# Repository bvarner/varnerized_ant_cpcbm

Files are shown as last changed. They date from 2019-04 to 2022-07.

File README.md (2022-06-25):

# Varnerized ANT Compact PCB Maker

Since first coming across the [ANT](https://www.youtube.com/channel/UCX44z-SSL7LzcB4xxgUdHHA) project, I've wanted to make one. However there are some esoteric hardware choices in the base project that seem to prioritize form over function and cost.
As a hobbiest, my primary concerns are not asthetics as much as cost and component availability.

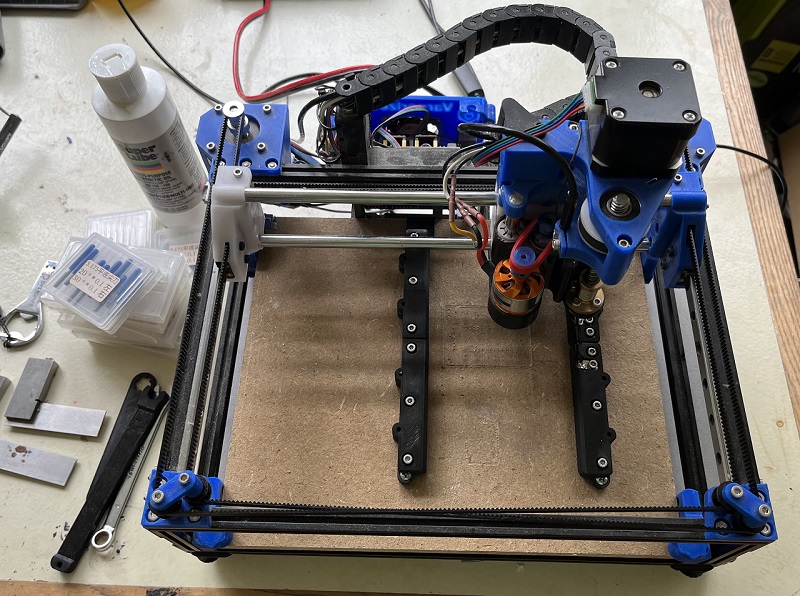
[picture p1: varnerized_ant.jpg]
Varnerized Ant


## Varnerizations
1. Created a parametric (parameterized) reimplemenation of the [bridge & head in Fusion 360](https://a360.co/3jG9QqE). Fusion Archive and STEP export included.
2. 8MM Linear Rods & LM8UU linear bearings. 
    * Sacrificed 4mm of Y axis travel to allow for wall thicknesses to be reasonable with 15mm bores.
    * Added 1mm to the height to the left-right bridge and center bridge, added 1mm separation betweeen centers of the x-axis rails.
3. Bridge Core is now One Piece.
    * Captive M3 Hex Nuts allow the use of (3) M3x30 and (3) M3x40 screws instead of the original BOM spec for (3) M3 threaded rods cut to length.
    * Linear bearing holes are _barely_ oversized, allowing for the M3x30 screws to act as compression mechanisms to hold the bearings.
    * Expansion / Compression cut for linear bearings. M3 screws holding together the bridge act as compression points to hold the bearings snug.
4. Use of sub-mini microswitches for limit-switches. No need to purchase specific orientation limit switch modules, especially when the connections to the grbl board aren't making use of pull resistors.
5. NEMA17 Stepper Motors
    * Reinforced COREXY Mounts based upon [this design on Thingiverse](https://www.thingiverse.com/thing:3590519) eliminate the need for extra retainers from the thingiverse part.
    * GT2 belt-driven Z-Axis. [140 Tooth 2GT-6](https://www.amazon.com/140-2GT-6-Timing-Belt-Closed-Loop/dp/B014QJBVOY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) allows for swapping out gear ratios to adjust for different leadscrew pitches.
6. TR8 Leadscrew (with 8mm pitch) for Z-Axis
7. Remodeled and removed unnecessary holes from the bridge left and right.
8. Belt holder holds a captive nut to secure it to the bridge.
9. Easily Obtainable [D2826 1000kv](https://www.amazon.com/dp/B089YPSYD6?psc=1&ref=ppx_yo2_dt_b_product_details) BLDC motor.
    * 3d-printed TPU (shore 95A) drive belt.
    * 3d-printed PolyCarbonate drive pulleys. (Eliminated the stop-collar on the spindle)
10. Use of an open cable chain, and necessary mounts to the bridge & electronics case.
    * Use of 40mm screws on the electronics case, further customizations to make it easier to fit panel-mount through-hole jacks.
    * modified the electronics panel to use a rectangular switch and a XT-60H connector for power.
11. 3d printed GT2 pulleys.
    * I have since switched to machine pulleys, as I was diagnosing some movement precision issues. Changing to machined pulleys had no noticeable effect. My issues were elsewhere.
12. PCBLock <-> Frame connection.
    * Changed orientation of the contact strips to vertical -- allowing for more 'slop' between alignment in both the x, and z axis.
    * Contact is no longer dependent upon the thickness of the spoil-board, so thinner / thicker board will still contact well.
    * I used 4mm strips of 0.15mm thick nickel strip. (cut from an 8mm wide strip commonly used in 18650 battery packs)

### Analysis and Evaulation Guidelines

In making my decisions about what to 'Varnerize' vs. purchase and stick to the plans I weighed things based upon:

* What's already in my component drawers or easily obtainable given current supply chain and production limitations. Prioritized functional available parts over form.
* What I can reasonably 3d-print and combine with something else already in my component drawers. Prioritized self fabrication over purchasing produced parts.
* Functional Accuracy. Modifications will prioritize accuracy over workable size. I was willing to reduce the work area. I didn't have to.
* Build cost.

### Specific investigations undertaken

* NEMA17 steppers in place of the NEMA11s, and in the case of the head, in place of the NEMA 8. I've seen [this top-mounted NEMA 11 modification](https://jplattel.nl/post/2021-03-07-improving-the-ant-head/) which has supplied a surprising amount of 'idea fuel'.
* Bridge segmenting and joinery.
* Use of an Arduino Uno R3 + GRBL board instead of the STM32 based Arm board + GRBL board.
* 8mm Rods and LM8UU bearings instead of the 6mm rods and LM6UU bearings.
* 3d printable pulleys based around 683ZZ bearings. As of 10/2021 I was able to obtain a 20 pack of these bearings for $10. Sourcing the appropirate number of 16-tooth pulleys would have cost more than the 20 pack of bearings.
* Overhangs in some parts (which seem to be dimensionally important) should have 'snap-off' supports.
* Use of a TR8x8 leadscrew, along with a GT2 closed loop belt and pulley system for Z-Axis motion. I have a few of these belts laying around from converting my prusa-style printer to a [Skelestruder](https://jltxplore.dozuki.com/c/Skelestruder_for_Prusa_MK3) extruder.

### Purchased items I did not 'skimp' on:
* MakerBeam! I bought the starter kit, and the tee nuts. I _did_ investigate printing the tee nuts and had workable facimilies printed with a 0.4mm nozzle but was not confident about the long-term use of the plastic tee-nuts.
* Linear rails. Experience from building 3d printers told me this was worth it.
* LM8UU Drylin Bushings. Because LM8UU ball bearings that are affordable are rubbish. I've been using drylin on my 3d printer for a year or so now, and it's so much quieter, and has so much less lash that it's just worth it.
* Mochu angular contact bearings & CL6-ER8M spindle.

#### Z-Axis Comparative Analysis
##### NEMA 8 ANT Head
The "Beta" NEMA 8 stepper head design uses a 1.8-degree, 18mN/m (0.018N/cm) holding torque stepper paired with a 4mm leadscrew with a 0.635mm pitch, equating to a 0.003175mm linear resolution per step.
(0.635mm / 200 steps = 0.003175mm). 

The default configuration is to set this to half-stepping, doubling the default ANT resolution to:
(0.635 / 400) = 0.0015875mm

##### NEMA 17 Varnerized Head
I have on hand several 17HS4401 steppers, which are 1.8-degree, 42N/cm holding torque, and TR8x8 leadscrews with 8mm pitch and anti-backlash nuts.
Un-reduced, this equates to a linear resolution of 0.04mm.
(8 / 200 = 0.04mm) 

In order to increase the resolution, I've selected a 16:52 gear ratio and 140 tooth GT2 timing belt (which I had on hand from building a Skelestruder extruder for my printer).
This brings the effective resolution to:
(8 / (200 * 3.25)) = 0.012307692mm

Enabling 1/4 stepping on the Z-axis motor brings this to:
(8 / (200 * 3.25 * 4)) = 0.003076923mm -- slighty better than the half-stepped NEMA 8.

Enabling 1/8 stepping on the Z-axis will yield:
(8 / (200 * 3.25 * 8)) = 0.001538462mm resolution -- on par with the half-stepped NEMA 8 head.

This equates to a theoretical steps/mm setting of: ~650 steps/mm

Assuming a loss of torque of 29% at the motor shaft (due to microstepping):
At the mottor shaft, the motor provides 29.82N/cm of holding torque.
(42 - (42 * 0.29))
At the lead-screw, this would be 3.25 times higher.
(29.82 * 3.25) = 89.46N/cm

**Conclusion**:

__With 1/8th microstepping, a 1:3.25 gear ratio, and an 8mm pitch leadscrew powered by a 17HS4401 NEMA17, we will exceed the repeatable resolution and torque of the ANT's NEMA8 head design.
Furthermore this part selection will enable using parts I have on hand, cutting the cost to build the head unit considerably.__

## Original ANT Project resources

(https://www.youtube.com/channel/UCX44z-SSL7LzcB4xxgUdHHA)  

The Ant is a project to develop a CNC machine able to realize single and double-layered printed circuit boards.

[Here is a video presentation](https://youtu.be/nVkbG-CYaAA)

The CNC machine is designed to achieve well-determined characteristics:

- Compact
- Low-cost
- Robust
- Scalable
- Easy to build
- Open License

To achieve these properties the following design principle have been adopted:

- Electrical, mechanical and electronics parts have been chosen to be small, low-cost and easily available on the open market or 3D printable
- Mechanical design has been oriented to minimize the space occupied by the components
- Mechanics has been designed to be robust and stress resistant
- Mechanics has been designed so that the external dimensions of the machine may be changed with a minimal change of pieces and no re-design needed.
- Mechanical and electrical designs have taken in account the assembling and disassembling operations, allowing to use easily available tools as screwdrivers, Allen wrenches and a solder for electrical contacts.
- The microcontroller board used to control the CNC machine is inexpensive (~15 $) but is equipped with a powerful STM32 processor and many peripherals.
- The machine control firmware can be loaded with almost no effort, since the microcontroller board has been chosen to have an on-board programmer.
- The control firmware is derived from GRBL v.0.9j, but it is also customized to achieve better performance, taking advantage of the powerful processor, and to be more flexible, since more configuration parameters and features have been added respect to the original firmware

The Ant is an open project, but if you feel like donating a small sum, you are very welcome. Just use the paypal button below.

paypal (https://www.paypal.com/cgi-bin/webscr?cmd=_s-xclick&hosted_button_id=BTRCVPZUZYW2E)

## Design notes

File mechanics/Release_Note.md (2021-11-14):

# 06-11-2021
New release The_Ant_version_1_1_0 with the new NEMA-8 motor as Z-axis. From now on, this head will be considered the stable version. List of updates:  

	* Total_BOM_Ver_1_1_0.xlsx:  
	    - Revisited version of the BOM that integrates the previous BOM with the new parts.

	* head_4p3 replaces head_4p2(copied in release folder from beta one):  
		- new head_4p3 that uses new Z-axis motor. See the BOM for the model of motor.  
	  
	* bridge_2p4_b replaces bridge_2p3_b(copied in release folder from beta one):  
	    - new bridge needed to accomodate the anti-backlash nut of the new Z-axis motor.
		
	* pcb_lock_2p3 replaces pcb_lock_1p0(copied in release folder from beta one):  
	    - the new pcb lock is more robust and adjustable.  
		- integrates part of probe circuit.  
		
	* pcb_lock_frame_to_bed_connection_1p0 added(copied in release folder from beta one):  
	    - new parts of the bed holder needed to integrate the new parts of probe circuit.  
		
	* cable_chain_1p0(copied in release folder from beta one):  
	    - new parts to use drag chain for the cable, substituting the spiral coil used previously.  

# 21-07-2019
New parts released, list of updates:

	* head_4p2 copied in release folder from beta one:
		- previous head_4p2 splitted in head_4p2 and pulley_4p2
		- pulley_4p2. It uses new collar for chuck pulley, if hexagon socket screw doesn't protude from the collar, replace it with a longer one. The file collects chuck pulley, turnigy pulley (3mm shaft) and mystery pulley (2.2mm shaft)
		- spindle motor with outer diameter up to 28mm can now be mounted.
	
	* bridge_2p3_a and bridge_2p3_b:
		- New version of the bridge, more rigid and stable.
		- The *_a it is file related at the unchanged parts from previous version. *_b file it's related to the new parts. They are fully compatible with the older version. If you have printed previous version, print only the *_b parts to update.
		- The bridge is compatible both with 4p1 and 4p2 head versions.
		- Added protection cap.
		- Modified camera holder, now more strong with new lock mechanism. 
		- Added lock holes at the bottom for future features.
		- Reinforced and updated z-motor connection.
	
	* z_motor_tool, useful tool to lock the z-motor shaft to the bridge.

Removed parts:

	* head_4p1
	
	* bridge_2p2

All previous parts are available in The_Ant_version_1_0_0 file.
You can find it in the download section under the "tags" tab.
A new version of BOM is added to keep trak of all changes.
The new pieces require a set of new parts:
	
	* 2 M3x10mm DIN 912 bolt
	* 1 M3x12mm DIN 912 bolt
	* 1 Lock collar(ring) internal diameter 6 mm, external diameter 12mm
	* 2 O-ring inner diameter > 17mm, 1.78mm thick. Innerd diameter to be defined.

# 23-04-2019
Added beta_developments directory, where we share parts not yet released and under test.

# 14-04-2019
Released all step files. 
Added tool for tool bit change (both stl and step).

Bug fixes:
bridge_2p2
	* minor bug fix, camera holder screw holes now deeper
	  to improve the clamping force
	  
head_4p1
	* minor bug fix, chuck pulley base now smaller to prevent
	  friction with bearing

# 31-12-2018

## Scope

Release of mechanical drawings of the Compact PCB Maker. 
This release completes the previous one and comprises the mechanical drawings of the bridge, of the head and of the microcontroller cover. 
The suggestions of the previous release apply also to this one.

# 09-12-2018

## Scope

First release of mechanical drawings of the Compact PCB Maker. 
This is a partial release that comprises all the frame related mechanical drawings. Other parts and corrections will follow in other releases.

## Suggestions

We suggest you to print the parts as they are, because the printing position is designed to enhance the mechanical behavior.

We also suggest you to print with a 0.2 mm layer thickness, 25% of infill, 1.5 mm of wall thickness and extrusion width (also called line width) of 0.5 mm. 

We usually print with PLA but it's not a MUST, you may choose different materials taking in account the properties of the material you want to use. The overall rigidity is needed.

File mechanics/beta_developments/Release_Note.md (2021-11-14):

# 06-11-2021
Removed all the beta parts that are now released in the new stable version The_Ant_version_1_1_0, and the old beta developments that were already obsolete.  

# 06-02-2021
Added <b>head_4p3</b>, an alternative head that uses the NEMA8.  
This head is meant to be used with the released <b>bridge_2p4_b</b> in which there is the anti backlash nut coupled with the motor.  
Added <b>pcb_lock_2p3</b>, an improved version of the previous 2p2.  
Added <b>cable_chain_1p0</b> to better organize the cables that connect the main electronics to the head electronics.  

# 23-04-2019
This is the Beta Developments folder where we share parts not yet released and under test.

Added <b>head_4p2</b>, an head modified to work with the Mistery D2632 blue and red version and brushless with up to 28 mm diameter.

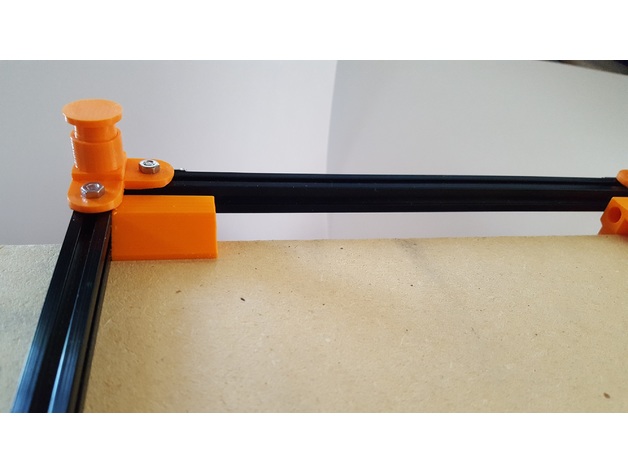
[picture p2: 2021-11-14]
mechanics/frame/Feet/images/b8899656f86f0776ce9d8ce595bd6f32_preview_featured.jpg

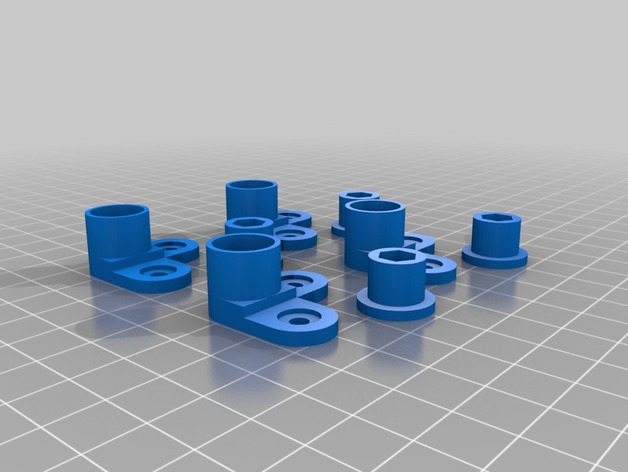
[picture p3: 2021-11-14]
mechanics/frame/Feet/images/fda94fc00cff2d6c941c1d48f293a349_preview_featured.jpg

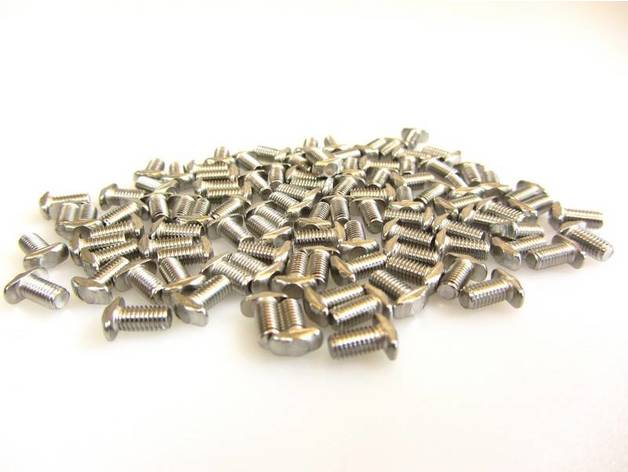
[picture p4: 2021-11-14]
mechanics/frame/Feet/images/6d514020f6163c7c261596526521b55e_preview_featured.jpg

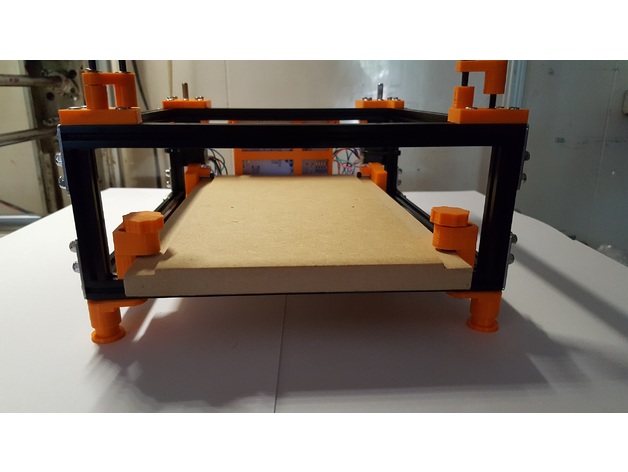
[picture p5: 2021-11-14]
mechanics/frame/Feet/images/d886d0a407164cc080b8dbe587c8e89c_preview_featured.jpg

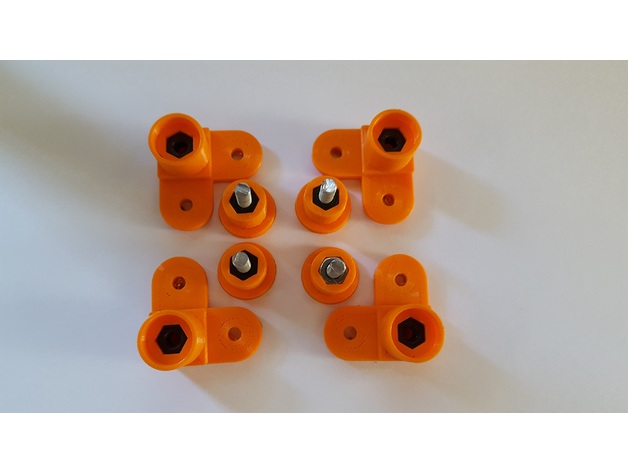
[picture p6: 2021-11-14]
mechanics/frame/Feet/images/ced9a25d92f1a28261a7ffedb2b2fa02_preview_featured.jpg

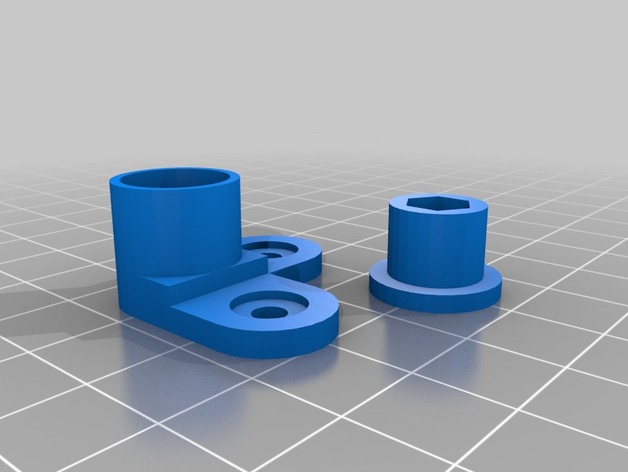
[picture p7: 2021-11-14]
mechanics/frame/Feet/images/ae2aa1dde648d54a71faf4bf8224e998_preview_featured.jpg

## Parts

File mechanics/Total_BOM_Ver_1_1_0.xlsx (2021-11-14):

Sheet: Important NOTE
This is the BOM of The Ant with the new parts released the 6th November 2021, that has the tag "The_Ant_version_1_1_0". If you want to download this frozen version, you may find the relative tag in the tags section of our repository: If you want to know which are the changes in the releases, please read the Release Note in the mechanics folder. | https://bitbucket.org/compactpcbmaker/cpcbm/downloads/?tab=tags

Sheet: Totals Frame BOM
Item | Video 1 | Video 2 | Video 3 | Video 4 | Video 5 | Video 6 | Ver. 1.0.1 | Ver. 1.1.0 | Qty | Info | removed parts
Makerbeam - 10x10mm aluminum profile 200mm (black) | 8 |  |  |  |  |  |  |  | 8 | Makerbeam
Makerbeam - 10x10mm aluminum profile 60mm (black) | 4 |  |  |  |  |  |  |  | 4 | Makerbeam
Makerbeam - 10x10mm aluminum Right Angle bracket | 8 |  |  |  |  |  |  |  | 8 | Makerbeam
M3x6mm square headed bolt | 47 |  |  |  |  |  |  | 9 | 56 | Makerbeam
ISO 7380 M3X4 A2 | 8 |  |  |  | 4 |  | 1 |  | 13 | Makerbeam
Makerbeam T-slot nut | 24 |  |  |  |  |  |  |  | 24 | Makerbeam
M3 self-locking nut | 46 | 9 |  | 2 |  |  |  |  | 57
M3 nut | 4 |  |  |  |  | 8 | 1 | 7 | 20
M5 nut |  |  |  | 1 |  | 2 |  | -1 | 2
M2x8mm DIN 7985 bolt |  |  |  |  | 2 |  |  |  | 2 | used to fix the z-limit switch (maybe you can use M2x10 DIN 7985 instead)
M2x10mm DIN 7985 bolt |  |  |  |  |  |  |  | 4 | 4
M2.5x8mm DIN 912 bolt |  |  |  | 8 |  |  |  |  | 8
M3x6mm DIN 912 bolt | 12 | 9 |  | 2 | 3 |  |  | 13 | 39
M3x8mm DIN 912 bolt |  |  |  |  | 4 |  |  | -2 | 2 | 2 bolts used to lock the nucleo in the case, maybe this can be replaced with 2 bolts M3x10 using double plastic washers (see video 5)
M3x10mm DIN 912 bolt |  | 4 |  |  |  | 8 | 2 | -6 | 8
M3x12mm DIN 912 bolt |  |  |  |  |  |  | 1 | 12 | 13
M3x16mm DIN 912 Bolt | 2 |  |  |  | 4 |  |  |  | 6
M3x20mm DIN 912 Bolt | 8 |  |  | 1 |  |  |  | 1 | 10
M3x25mm DIN 912 bolt |  |  |  | 2 |  |  |  |  | 2
M3x30mm DIN 912 Bolt | 4 |  |  |  |  |  |  |  | 4
M3x50mm DIN 912 bolt |  | 2 |  |  | 4 |  |  |  | 6
M5x16mm hexagon head bolt |  |  |  |  |  | 2 |  |  | 2
Wood screws 3x16mm |  |  |  |  |  | 6 |  | 1 | 7
M3 locking Washer (internal diameter 3mm, external 5.5mm) | 8 | 14 |  |  |  |  |  |  | 22
M3 Washer (internal diameter 3mm, external 7.5mm) | 16 | 10 |  |  |  |  |  |  | 26
GT2 pulley 16T Bore 3mm with bearings | 4 | 2 |  |  |  |  |  |  | 6 | Aliexpress
GT2 pulley No Teeth Bore 3mm with bearings |  | 2 |  |  |  |  |  |  | 2 | Aliexpress
GT2 pulley 16T Bore 5mm height 10mm |  |  |  | 2 |  |  |  |  | 2 | Aliexpress
GT2 6mm Timing belt piece 100 cm |  |  |  | 2 |  |  |  |  | 2 | Aliexpress
Timing Belt Tensioner Spring | 2 |  |  |  |  |  |  |  | 2 | SKU135539-3 FFIO PCK
MGN9H Linear Rail 200 mm | 2 |  |  |  |  |  |  |  | 2 | Aliexpress or Banggood
Bearings lm6uu |  | 8 |  |  |  |  |  |  | 8 | Amazon
Bearing mochu 706C |  | 2 |  |  |  |  |  |  | 2 | Aliexpress
Chrome Plated Rods 6x180mm |  | 2 |  |  |  |  |  |  | 2 | Aliexpress (can be 6x200mm)
Chrome Plated Rods 6x100mm |  | 2 |  |  |  |  |  |  | 2
Threaded Rods M3x100mm |  | 3 |  |  |  |  |  |  | 3
Mechanical Limit Switch Module Vertical |  | 2 |  |  |  |  |  |  | 2 | Aliexpress
Mechanical endstop micro switch with dupont terminal |  |  | 1 |  |  |  |  |  | 1 | Aliexpress
ER8M-C6-60L chuck with 1/8" spring collet |  |  |  | 1 |  |  |  |  | 1 | Aliexpress
~~Lock collar(ring) internal diameter 6 mm, external diameter 12mm~~ |  |  |  | ~~1~~ |  |  |  |  | ~~1~~ | ~~Amazon or Aliexpress. The measured external diameter is 13mm~~
Lock collar(ring) internal diameter 6 mm, external diameter 12mm |  |  |  |  |  |  | 1 |  | 1 | Amazon or Aliexpress. The measured external diameter is 12mm
~~O-ring inner diameter 17mm, 1.78mm thick~~ |  |  |  |  |  | ~~2~~ |  |  | ~~2~~
O-ring inner diameter > 17mm, 1.78mm thick |  |  |  |  |  |  | 2 |  | 2 | Inner diameter to be comfirmed
NEMA-11 JK28HS51-674 |  |  | 2 |  |  |  |  |  | 2 | Aliexpress or Banggood
NEMA 8 with 70mm lead screw 8HY001-70N476 |  |  |  |  |  |  |  | 1 | 1 | Available on Robotdigg site. IMPORTANT NOTE: This line refers only to the stepper motor, not to the anti-backlash nut that must be purchased separately (see the relative line in this file). To buy this motor on the Robodigg page, select the 8HY001-70N476 and put it in the cart. https://www.robotdigg.com/product/644/NEMA8-Linear-Stepper-Motor-with-lead-screw-Tr4.76-or-Tr5
Anti-Backlash Nut ABN476_0635 |  |  |  |  |  |  |  | 1 | 1 | Available on Robotdigg site. IMPORTANT NOTE: This line refers only to the anti-backlash nut, not to the stepper motor that must be purchased separately (see the relative line in this file). To buy this nut on the Robodigg page, select the ABN476_0635 and put it in the cart. https://www.robotdigg.com/product/644/NEMA8-Linear-Stepper-Motor-with-lead-screw-Tr4.76-or-Tr5
~~Z axis motor LC1574W-04-025~~ |  |  |  | ~~1~~ |  |  |  |  | ~~1~~
~~M12 nut with step 1.75mm, 5mm thick~~ |  |  |  | ~~1~~ |  |  |  |  | ~~1~~ | ~~This should be sold with the Z-axis motor, if not use the correspondant 3D printed part.~~
2632 brushless outrunner motor 1000 kV |  |  | 1 |  |  |  |  |  | 1 | Turnigy on HobbyKing or Mistery on Aliexpress. The latter is still not tested and requires different head pieces
ESC AFRO 20A or Afro 20A Race Spec Mini ESC with BEC |  |  | 1 |  |  |  |  |  | 1 | HobbyKing If you use the Afro 20 Race Spec Mini ESC you may need to substitute the 2 mm bullet connectors with 3.5 mm ones (3 females for the motor, 2 males for power supply).
Nucleo F401RE |  |  |  |  | 1 |  |  |  | 1
CNC arduino shield V3 |  |  |  |  | 1 |  |  |  | 1
Stepstick stepper driver |  |  |  |  | 3 |  |  |  | 3
Male 3.5 bullet connectors |  |  | 3 |  |  |  |  |  | 3
Female 3.5mm bullet connectors |  |  | 2 |  |  |  |  |  | 2
Male connector JST PH 2.0 1x04 pins |  |  | 1 |  |  |  |  |  | 1
Female Dupont connector 1x04 |  |  | 2 |  |  |  |  |  | 2
Female Dupont pin |  |  | 14 |  |  |  |  |  | 14
Female Dupont connector 1x03 |  |  | 2 |  |  |  |  |  | 2
Female Dupont connector 1x01 |  |  |  |  |  |  |  | 2 | 2 | To Connect bed probe GND and 5V (see pcb_lock_connections_schematic.pdf)
~~Crocodile clips with plastic covers~~ |  |  | ~~2~~ |  |  |  |  |  | ~~2~~
Extension Servo Lead Wire Male to Female 15 cm cable |  |  | 1 |  |  |  |  |  | 1
~~Stereo earphone with jack 3.5mm~~ |  |  | ~~1~~ |  |  |  |  |  | ~~1~~
Cable 26 AWG about 50 cm |  |  | 4 |  |  |  |  | 2 | 6 | Used for Z-axis stepper motor connector and head probe
Cable 16 AWG about 50 cm |  |  | 2 |  |  |  |  |  | 2 | Used for ESC power supply connection
Cable 16AWG about 30cm |  |  |  |  | 2 |  |  |  | 2
Dupont cable Female to Female 30 cm |  |  |  |  | 2 |  |  |  | 2
Pieces of heat shrink tube |  |  |  |  |  |  |  |  | 0 | Various with different sizes
Small zip ties |  |  |  | 4 |  |  |  | 1 | 5
2.54mm jumper |  |  |  |  | 10 |  |  |  | 10
~~Sheath spiral tube 6 mm about 1 m~~ |  |  |  |  | ~~1~~ |  |  |  | ~~1~~
MDF wood board 240x150x10mm (LxWxH) |  |  |  | 1 |  |  |  |  | 1
12V on-off round switch with 14mm mounting hole |  |  |  |  | 1 |  |  |  | 1
Panel mount DC power jack inner diameter 2.5mm external diameter 5.5mm |  |  |  |  | 1 |  |  |  | 1
~~Panel mount 3.5mm mono female headphone plug~~ |  |  |  |  | ~~1~~ |  |  |  | ~~1~~
12V brushless 40x40x10mm fan |  |  |  |  | 1 |  |  |  | 1
12V 10A power supply |  |  |  |  |  | 1 |  |  | 1
Cable Drag Chain 10x20mm outer dimensions, 7x15 inner dimensions ~30cm with heads |  |  |  |  |  |  |  | 1 | 1 | IMPORTANT NOTE: if you want add chain to your Ant with Bridge b version < 2p4, you may drill 2 holes (with 2.8mm of diameter) to the bridge.
Brass Foil thickness 0.1mm |  |  |  |  |  |  |  | 1 | 1 | To have an idea of the required area see pcb_lock_brass_foil_jig.pdf
Ring crimping terminal with ID 3mm |  |  |  |  |  |  |  | 2 | 2 | To Connect bed probe to terminals (see pcb_lock_connections_schematic.pdf)
LED 5mm |  |  |  |  |  |  |  | 1 | 1 | (see pcb_lock_connections_schematic.pdf)
0.25W 330 Ohms Resistor through hole |  |  |  |  |  |  |  | 1 | 1 | (see pcb_lock_connections_schematic.pdf)

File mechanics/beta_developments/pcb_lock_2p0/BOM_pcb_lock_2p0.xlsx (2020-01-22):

Item | Qty
M3x6mm square headed bolt | 2
M3 Washer (internal diameter 3mm) | 12
M3x10mm DIN 912 bolt | 21
M3 nut | 14
Female Dupont connector 1x01 | 2
Wood screws 3x16mm | 7
Brass foil thickness 0.1mm | 1
Cable ~ 26AWG about 50cm | 1
Ring crimping terminal with ID 3mm | 2
MDF wood board 240x150x10mm (LxWxH) | 1
LED 5mm | 1
0.25W 330 Ohms Resistor through hole | 1
Important NOTE: if you already built the old PCB holder you may re-use part of the pieces of the old PCB holder in the new one. This BOM counts all the pieces needed for the new PCB holder, indipendently from the other BOMs.

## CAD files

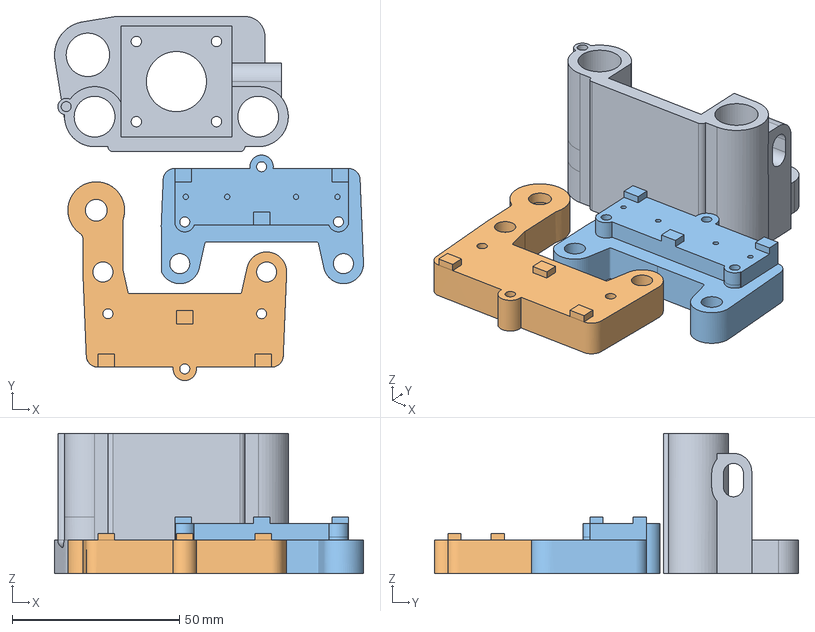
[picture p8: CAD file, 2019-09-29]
mechanics/cutterpilla/bridge_and_head_assembly_print_1p0.step
92.5 x 109.0 x 42.0 mm

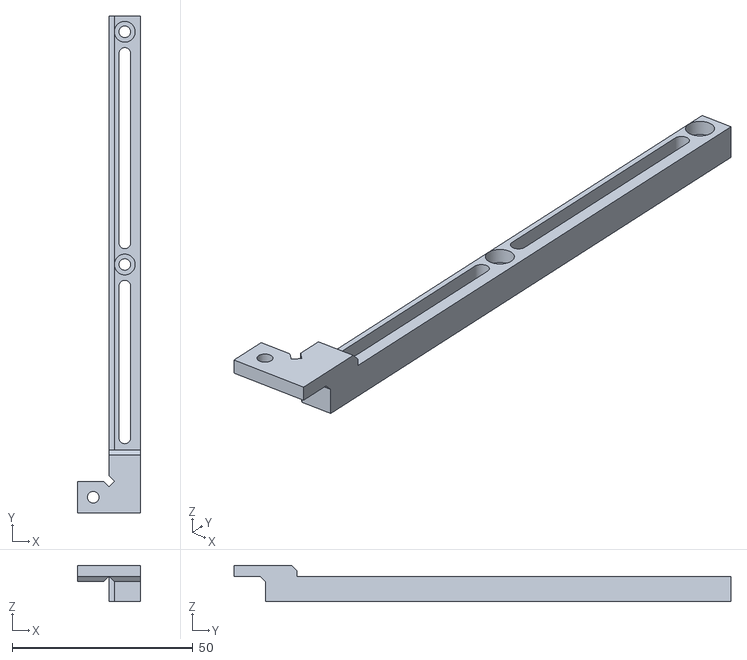
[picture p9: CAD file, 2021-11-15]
mechanics/bed/Right Bracket.stl
17.5 x 137.5 x 10.0

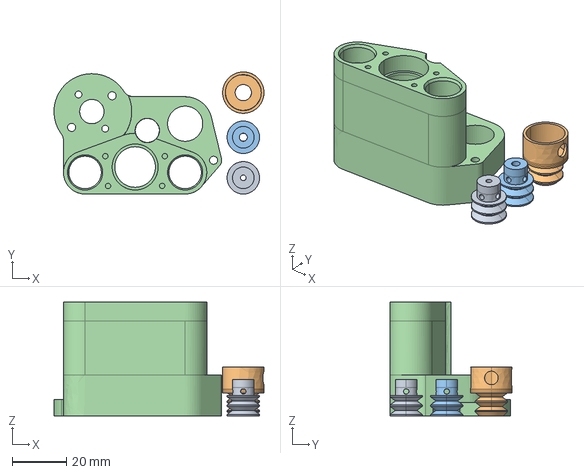
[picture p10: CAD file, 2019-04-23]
mechanics/beta_developments/head_4p2_beta.stp
77.6 x 45.1 x 42.0 mm

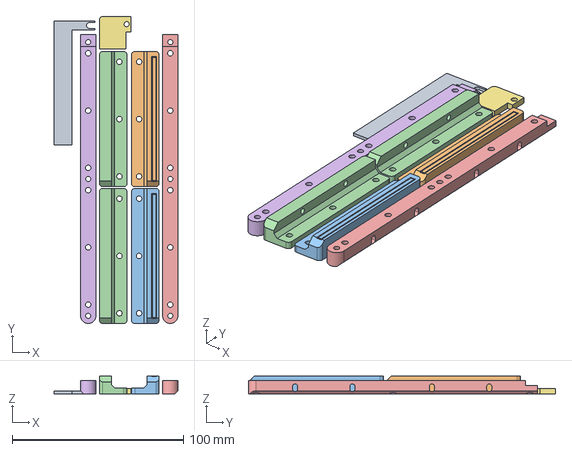
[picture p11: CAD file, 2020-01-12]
mechanics/beta_developments/pcb_lock_2p0/pcb_lock_2p2.step
72.5 x 179.5 x 10.3 mm

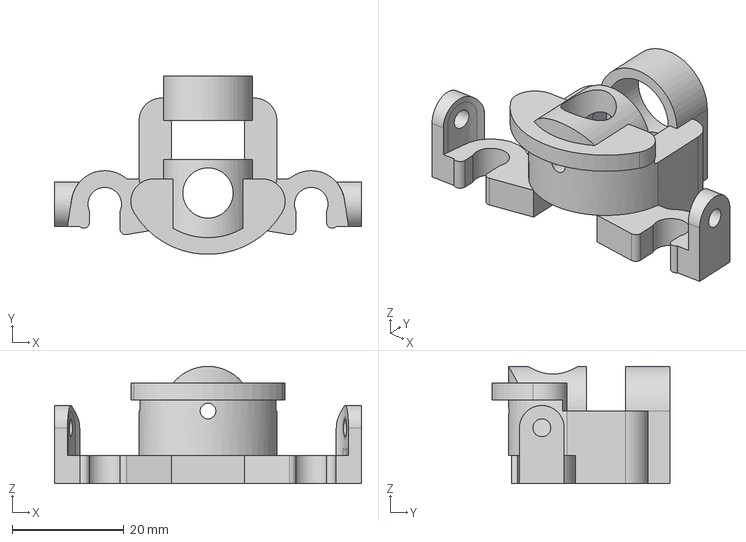
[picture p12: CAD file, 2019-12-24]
mechanics/beta_developments/Solder_Mask_Add_On/laser_soldermask_beta_1p0.step
55.0 x 32.0 x 21.0 mm

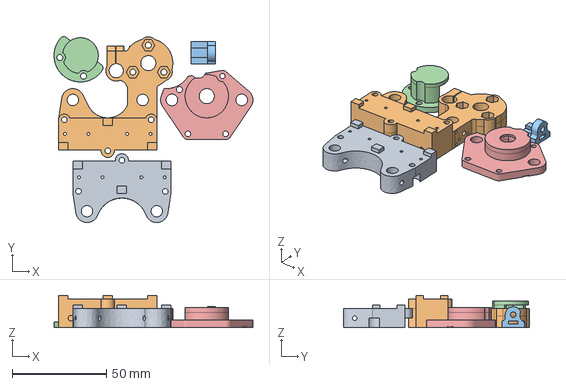
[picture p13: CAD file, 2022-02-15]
mechanics/bridge/bridge_2p4_b.stp
105.5 x 98.6 x 17.0 mm

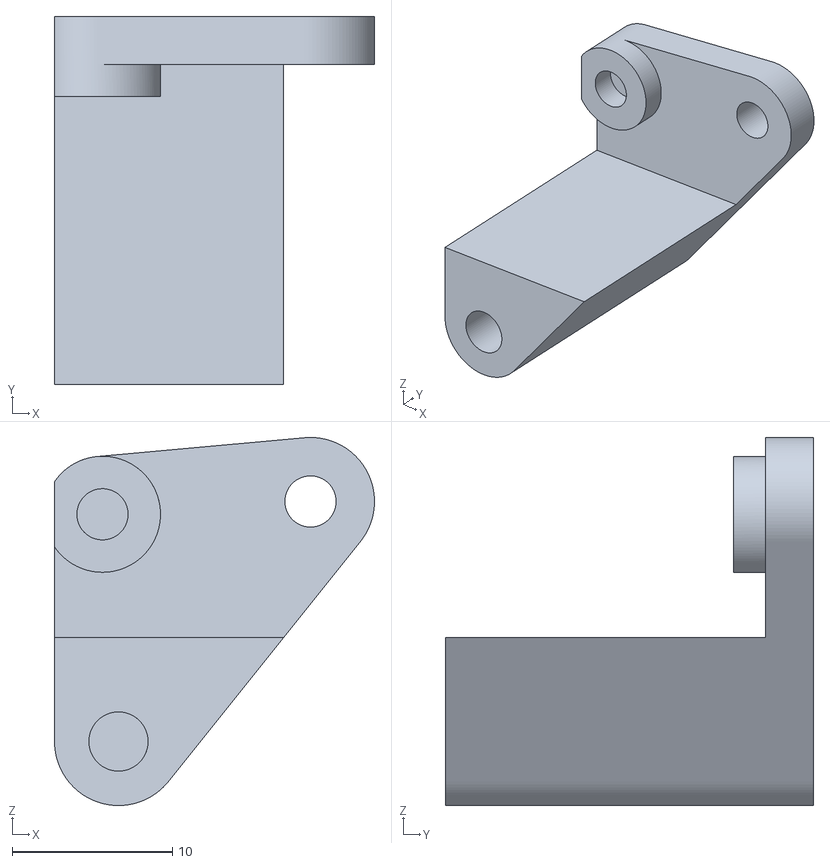
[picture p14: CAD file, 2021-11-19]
mechanics/electronics_and_accessories/OpenCableChain/Bridge Anchor.stl
20.0 x 23.0 x 23.0

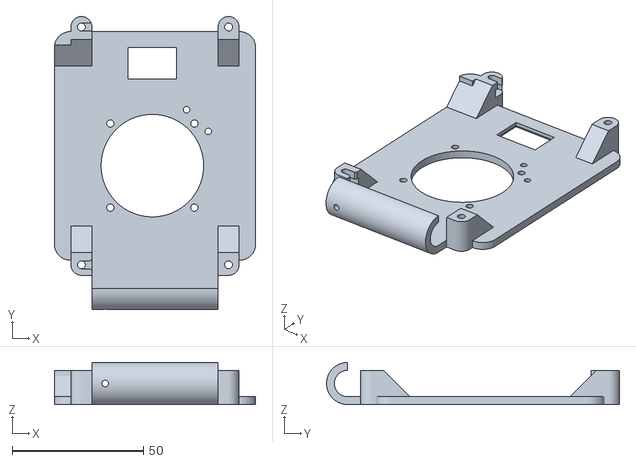
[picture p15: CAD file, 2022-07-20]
mechanics/electronics_and_accessories/varnerized_nucleo_cover_1p4.stl
76.5 x 111.5 x 16.0

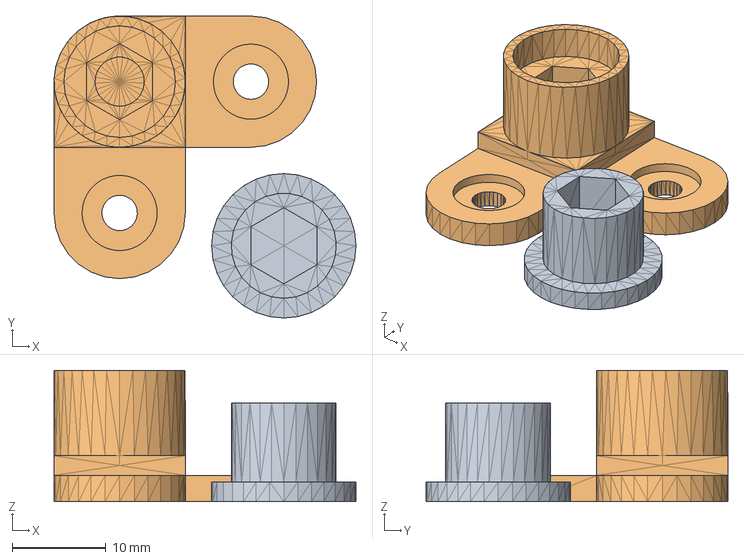
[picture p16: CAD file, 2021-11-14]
mechanics/frame/Feet/files/Ant__Compact_PCB_Maker_Adjustable_Feet_.iges
32.2 x 32.2 x 14.0 mm

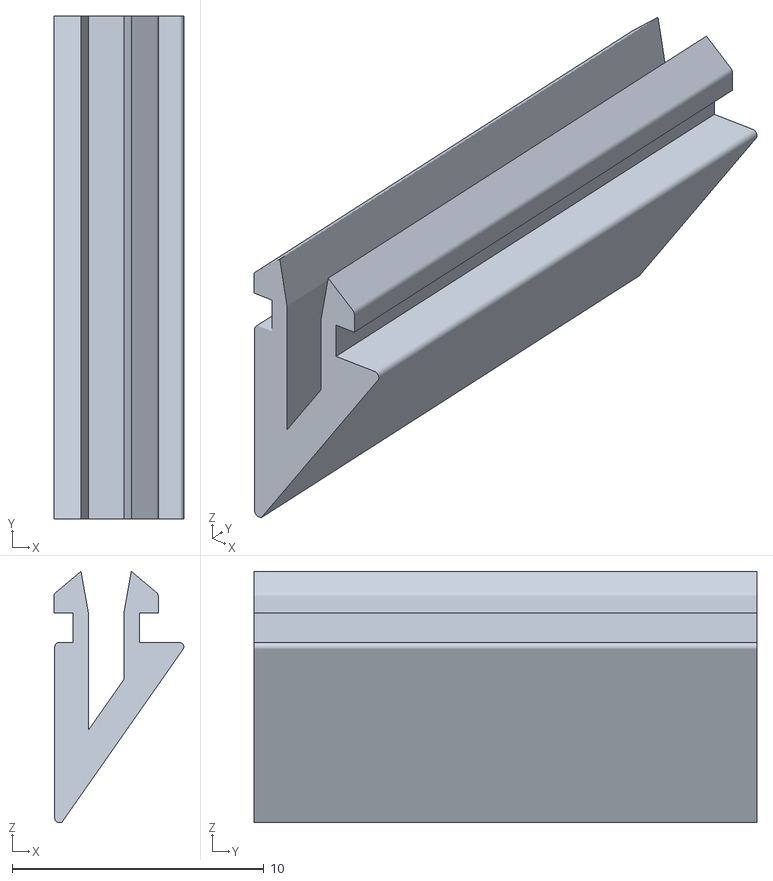
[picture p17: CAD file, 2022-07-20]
mechanics/frame/LED Clip.stl
5.16 x 20.0 x 9.99

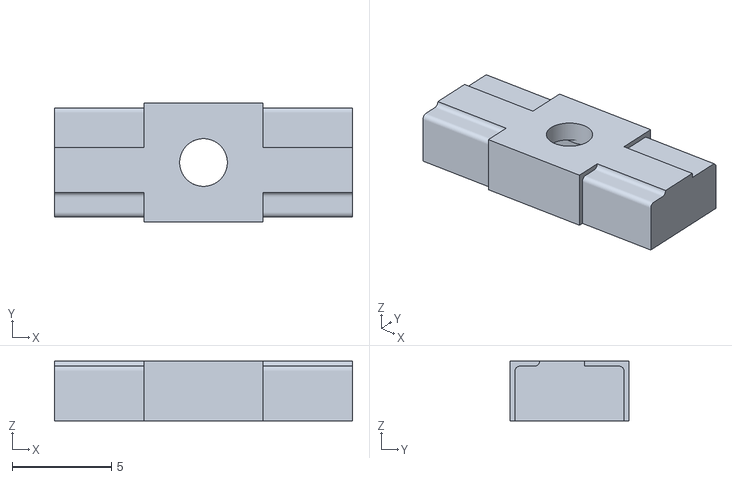
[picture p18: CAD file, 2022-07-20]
mechanics/frame/spoilboard/BedContactorFoilRetainer.stl
15.0 x 6.00 x 3.00

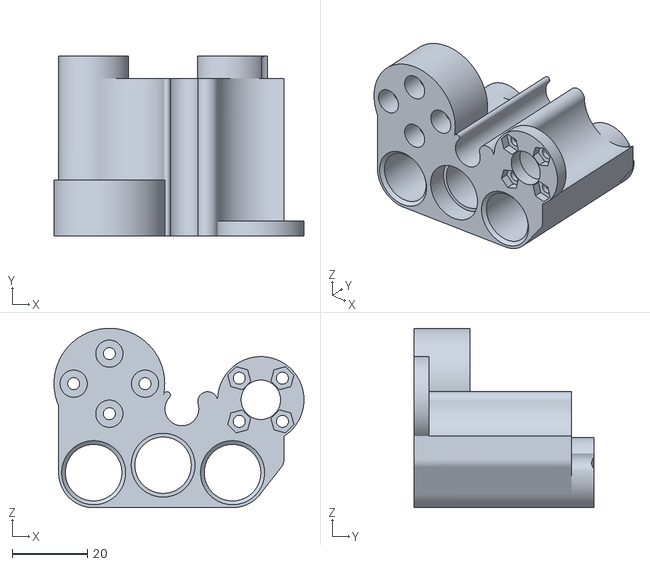
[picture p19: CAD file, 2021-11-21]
mechanics/head/head_8mm_D2826_TR8.stl
66.6 x 48.0 x 47.8

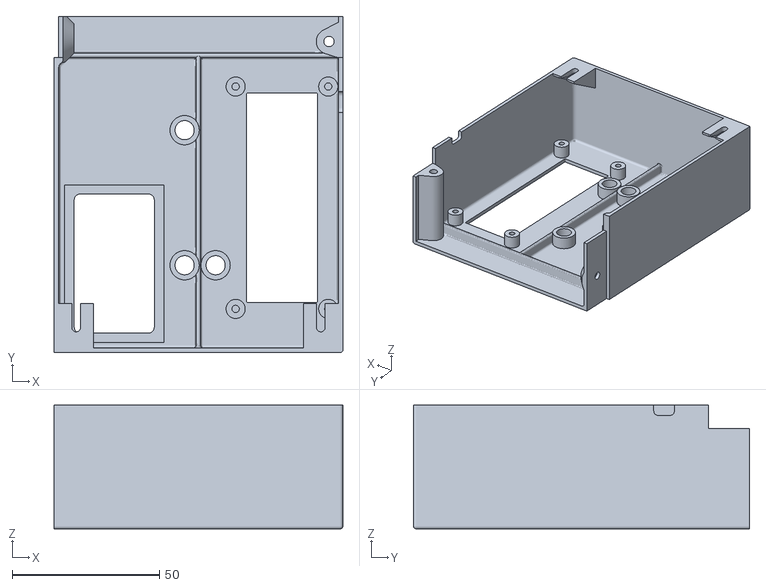
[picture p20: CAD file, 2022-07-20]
UVLEDController/PSU Shroud.stl
98.0 x 114.0 x 42.0

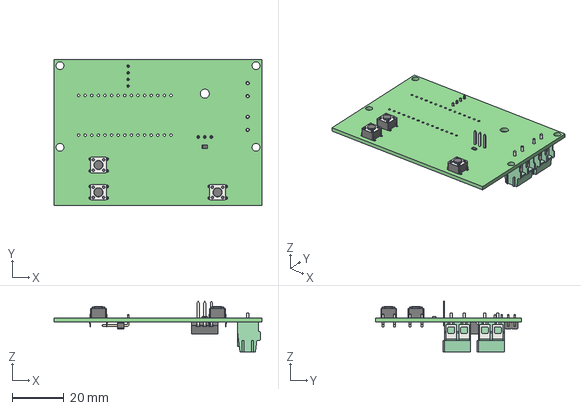
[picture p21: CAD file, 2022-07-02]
UVLEDController/UVLEDController/UVLEDController.step
80.0 x 56.0 x 19.5 mm
UVLEDController PCB

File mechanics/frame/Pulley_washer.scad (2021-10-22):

$fn = 360;

difference() {
    cylinder(d = 5.5, h = 0.5);
    translate([0, 0, -0.25]) cylinder(d = 3.2, h = 1);
}

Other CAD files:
mechanics/bed/HoldDown.stl
mechanics/bridge/bridge_nema17_mount_tr8.3mf
mechanics/electronics_and_accessories/OpenCableChain/CableChain_FrameMount.stl
mechanics/electronics_and_accessories/Support1.stl
mechanics/frame/Pulley_T-MXL-XL-HTD-GT2_N-tooth.scad
UVLEDController/Button.stl
UVLEDController/Standoff.stl
mechanics/bed/Front Bracket.stl
mechanics/beta_developments/Solder_Mask_Add_On/laser_soldermask_beta_1p0.stl
mechanics/beta_developments/head_4p2_beta.stl
mechanics/beta_developments/pcb_lock_2p0/pcb_lock_2p2.stl
mechanics/bridge/belt_holder.3mf
mechanics/bridge/belt_holder.stl
mechanics/bridge/belt_tensioner_lower.stl
mechanics/bridge/belt_tensioner_upper.stl
mechanics/bridge/bridge_2p3_a.stp
mechanics/bridge/bridge_2p4_b.stl
mechanics/bridge/bridge_core_8mm.3mf
mechanics/bridge/bridge_core_8mm.stl
mechanics/bridge/bridge_lower_8mm.3mf
mechanics/bridge/bridge_lower_8mm.stl
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

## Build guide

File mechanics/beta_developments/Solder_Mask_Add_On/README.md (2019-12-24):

# LICENSE

The method to cure the solder mask selectively with a laser is an idea of The Ant Team, and it is released with license CC BY-NC-SA 4.0.

Please, refer to the following link to know the details about this license.



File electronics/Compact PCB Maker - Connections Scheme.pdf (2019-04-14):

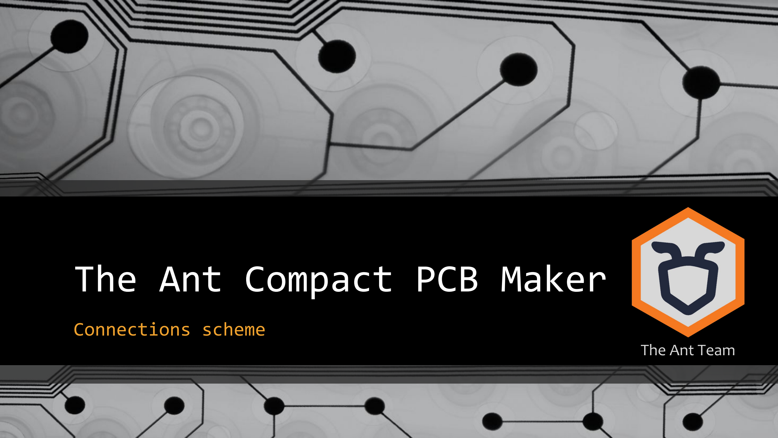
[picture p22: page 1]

# The Ant Compact PCB Maker

### Connections scheme

The Ant Team

# Introduction

## This document shows how to connect the different electronics parts of The Ant Machine. We strongly suggests you to watch these videos:

## https://youtu.be/eRefCvD_KVs

as a preparation for this stage of machine construction,

## https://youtu.be/ptuefynbbEo

as connection instructions.

# Electronics central unit parts

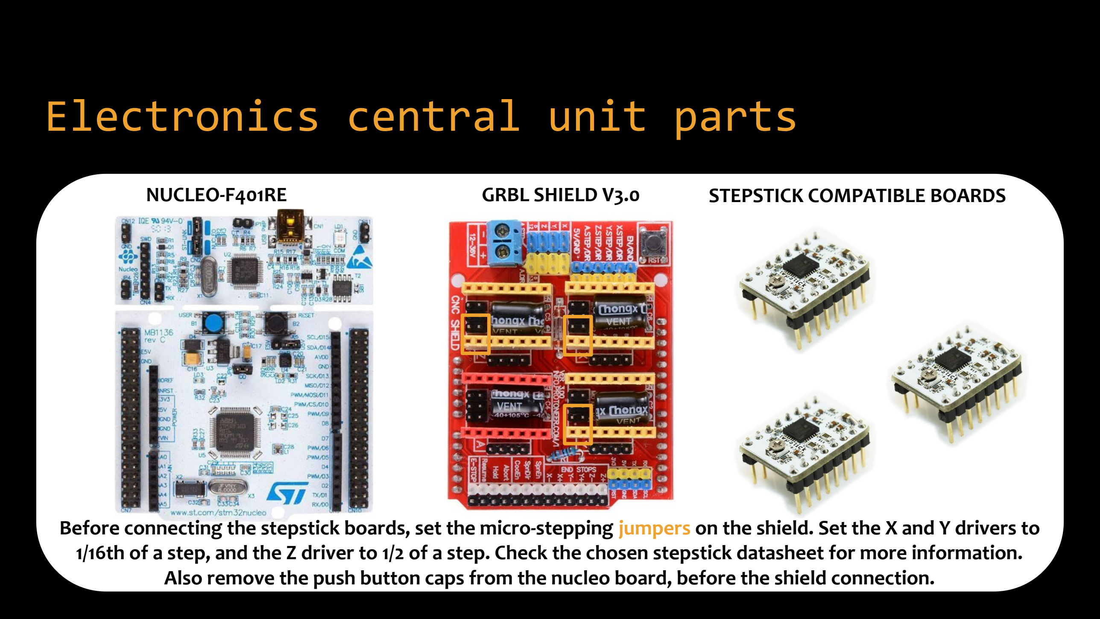
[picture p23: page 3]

Before connecting the stepstick boards, set the micro-stepping jumpers on the shield. Set the X and Y drivers to 1/16th of a step, and the Z driver to 1/2 of a step. Check the chosen stepstick datasheet for more information. Also remove the push button caps from the nucleo board, before the shield connection.

NUCLEO-F401RE | GRBL SHIELD V3.0 | STEPSTICK COMPATIBLE BOARDS

# Power Supply

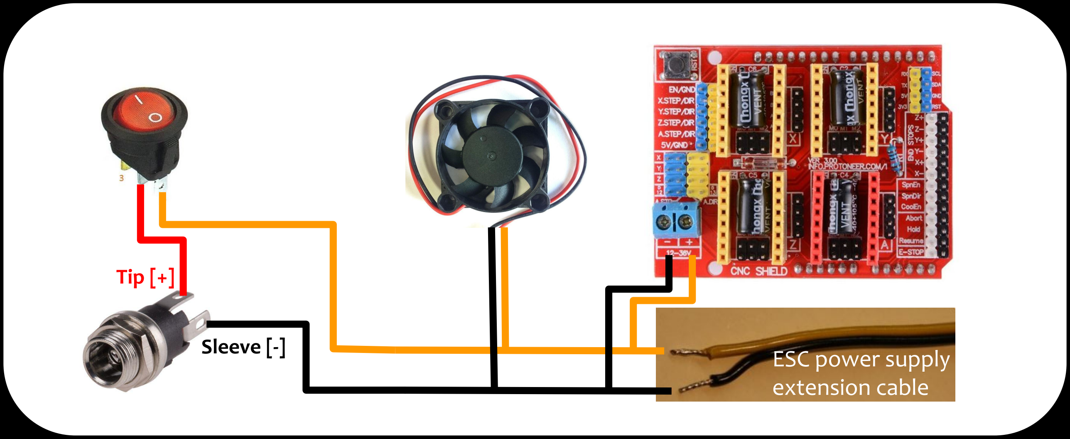
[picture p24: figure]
ESC power supply extension cable; Sleeve [-]; Tip [+]

# ESC Power Supply

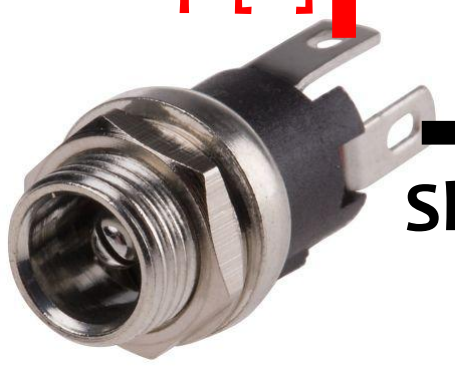
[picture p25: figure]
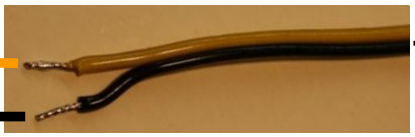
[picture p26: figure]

Sleeve [-]

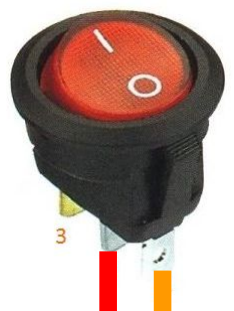
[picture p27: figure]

Tip [+]

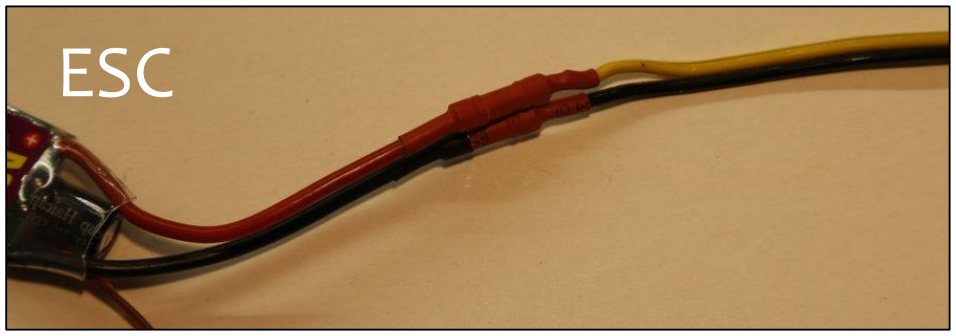
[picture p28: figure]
ESC

# CoreXY Stepper Motors

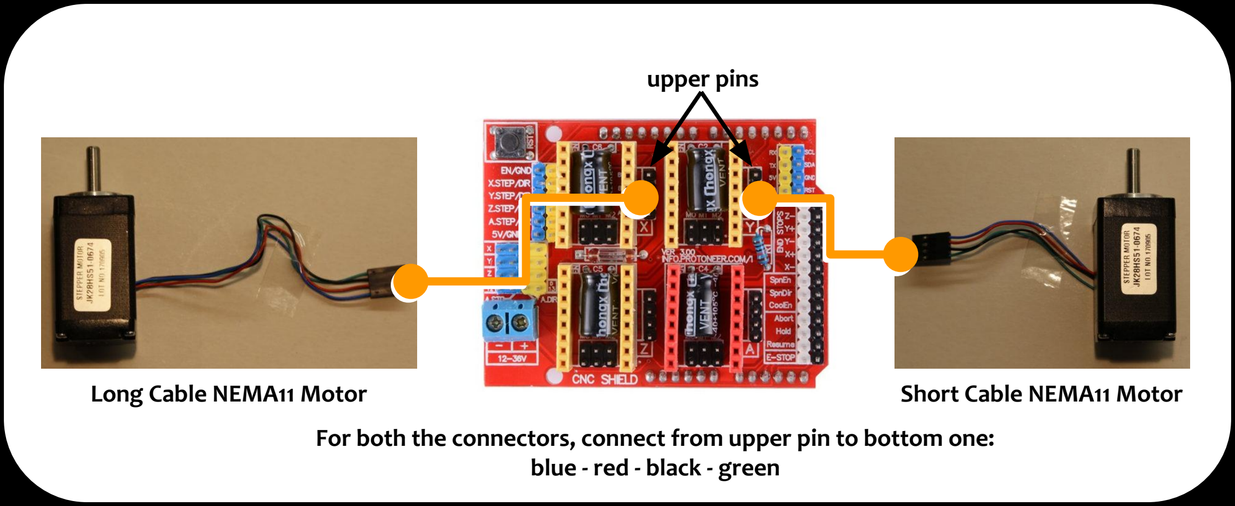
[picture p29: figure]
blue - red - black - green; upper pins; Long Cable NEMA11 Motor; Short Cable NEMA11 Motor

For both the connectors, connect from upper pin to bottom one:

# Z axis Stepper Motor

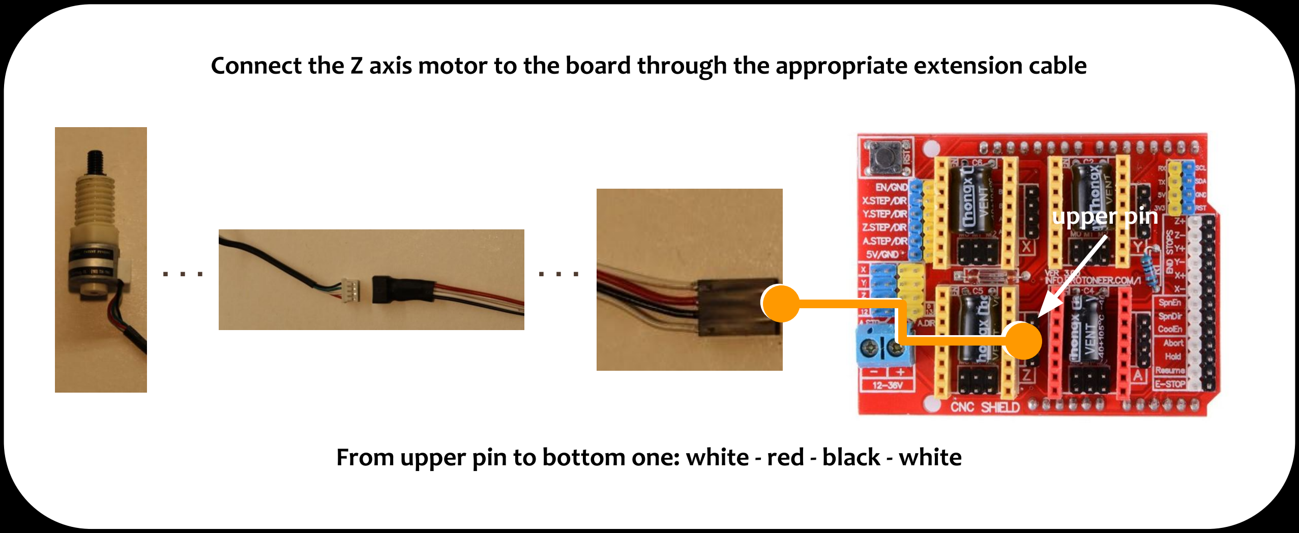
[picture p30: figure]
upper pin

From upper pin to bottom one: white - red - black - white

Connect the Z axis motor to the board through the appropriate extension cable

# Z axis Limit Switch

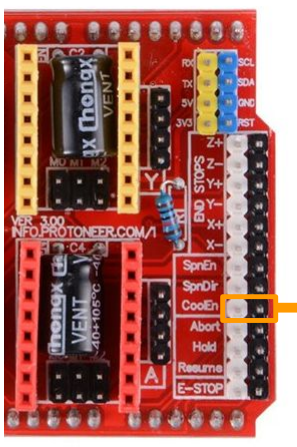
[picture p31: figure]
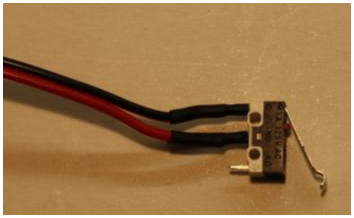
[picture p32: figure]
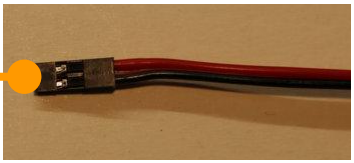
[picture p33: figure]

Black ground wire connected to the right pin, signal red wire connected to the left pin

# Y axis Limit Switch

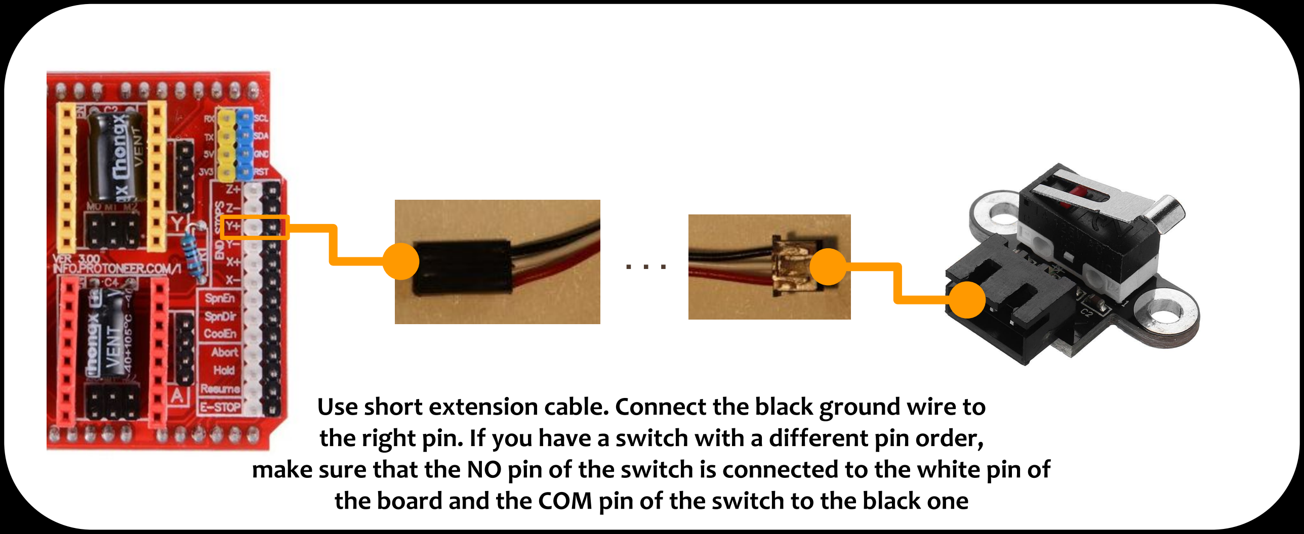
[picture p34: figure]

Use short extension cable. Connect the black ground wire to the right pin. If you have a switch with a different pin order, make sure that the NO pin of the switch is connected to the white pin of the board and the COM pin of the switch to the black one

# X axis Limit Switch

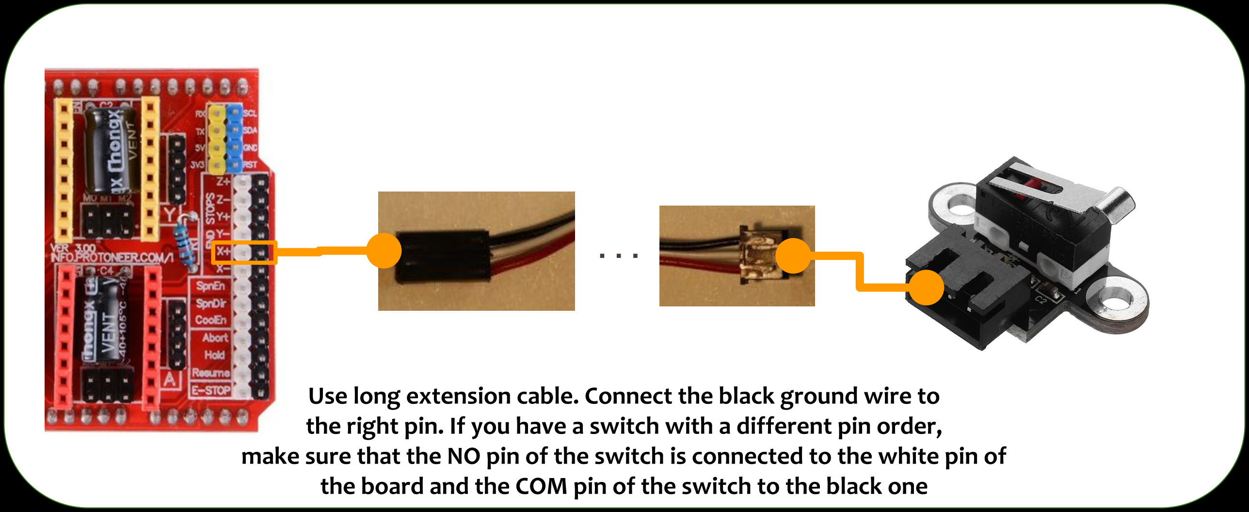
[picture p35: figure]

Use long extension cable. Connect the black ground wire to the right pin. If you have a switch with a different pin order, make sure that the NO pin of the switch is connected to the white pin of the board and the COM pin of the switch to the black one

# Spindle PWM control

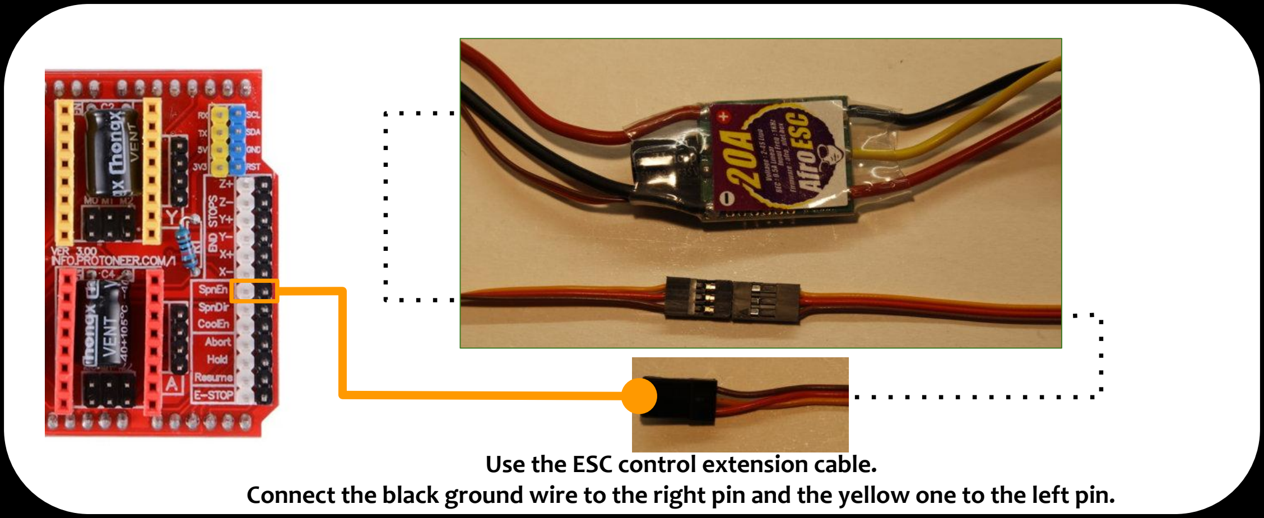
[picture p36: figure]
Use the ESC control extension cable.

Connect the black ground wire to the right pin and the yellow one to the left pin.

# Spindle ESC to brushless

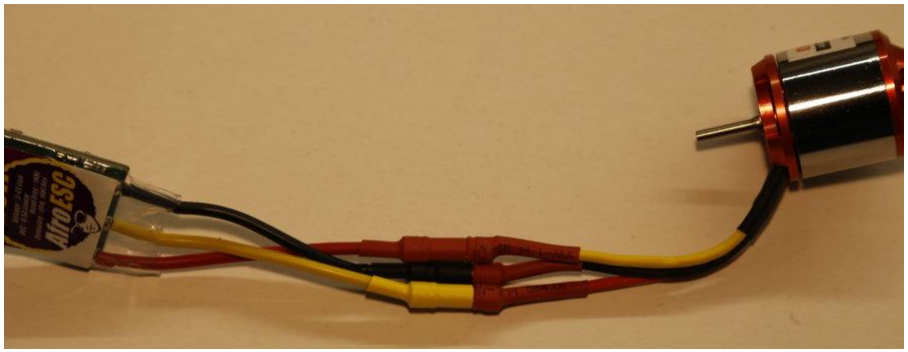
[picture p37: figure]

Check the connections. For our configuration Red and Yellow wire must be inverted. The machining bit has to spin clockwise looking at it from the top of the machine.

# Probe jack connector

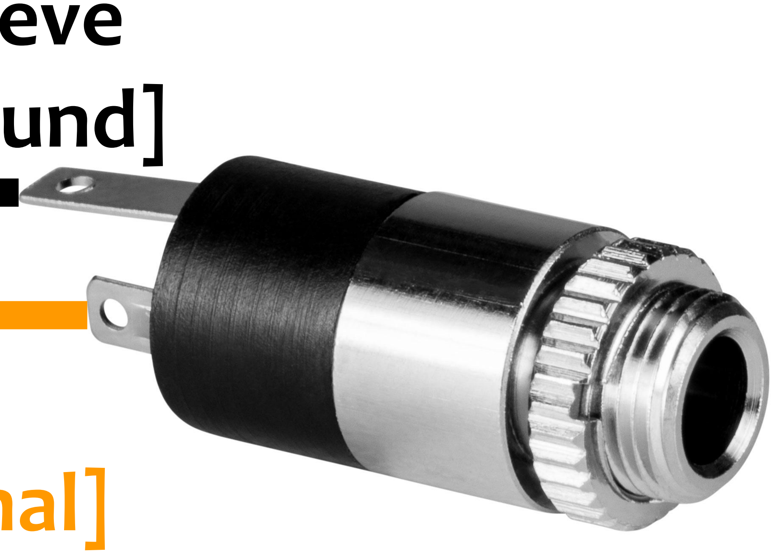
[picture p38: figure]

Sleeve
[ground]

Tip
[probe signal]

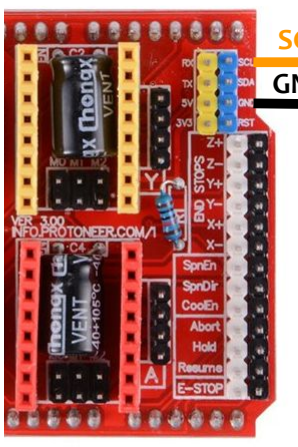
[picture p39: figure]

SCL
GND

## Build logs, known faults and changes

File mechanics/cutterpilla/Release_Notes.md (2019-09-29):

# 28-09-2019
LASER HEAD ADD-ON

[Related video presentation](https://youtu.be/V-mHSj8K_-w)

In this folder you can find all the necessary files to make
the laser head holder: the head holder and two carriage
mods.
The pieces fit a FB03-2500 laser head, an EleksMaker PWM
capable, 2500mW Blue Laser Module and related clones.  

All mechanical pieces are included in the main project BOM
except the 4 screws needed to fix the laser head.
We used 4 M3x8mm DIN 912 bolt, but longer bolts could be
used.  

In the sub-folder gcode, you can find two different demo
codes. The first is a 40x40mm Bud Spencer Clip Art, the second
one is just a 40x40mm rectangle useful to try different
combination of engraving settings, like feedrate (F command)
and laser power (S command) that has a range from 0 to 1000.  

The settings changed respect to the default settings for The Ant 
Compact PCB Maker are the following:  

$28=500 (Spindle pwm period, us)  
$29=499 (Spindle pwm Max time-on, us)  
$30=0 (Spindle pwm min time-on, us)  
$31=1 (Spindle pwm Enabled at startup)  
 
$110=3500.000 (x max rate, mm/min)  
$111=3500.000 (y max rate, mm/min)  
$112=500.000 (z max rate, mm/min)  
$120=30000.000 (x accel, mm/sec^2)  
$121=30000.000 (y accel, mm/sec^2)

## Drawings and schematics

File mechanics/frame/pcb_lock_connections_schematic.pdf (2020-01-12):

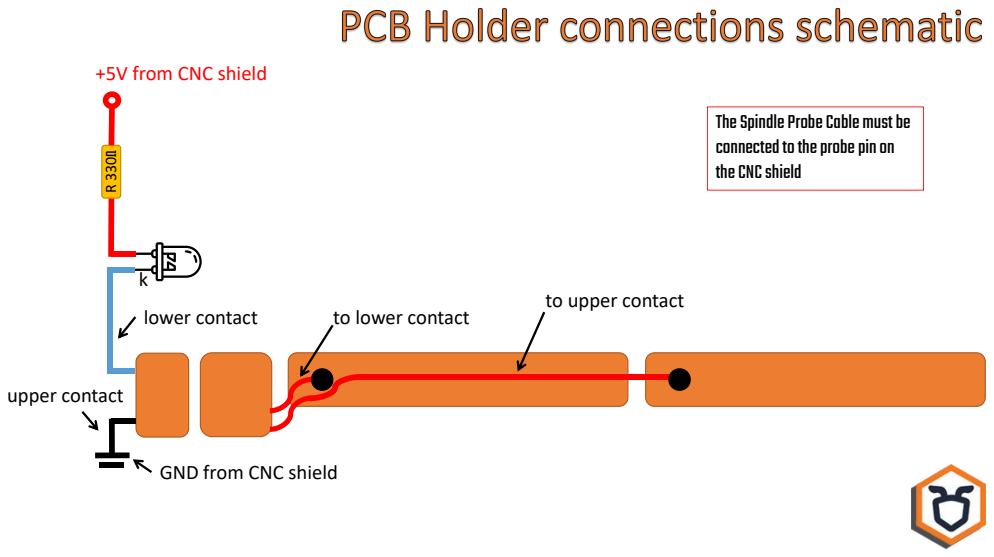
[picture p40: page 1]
lower contact; upper contact; TheSpindleProbeCable mustbe connectedtotheprobepinon theCNCshield

+5V from CNC shield

to upper contact

to lower contact

GND from CNC shield

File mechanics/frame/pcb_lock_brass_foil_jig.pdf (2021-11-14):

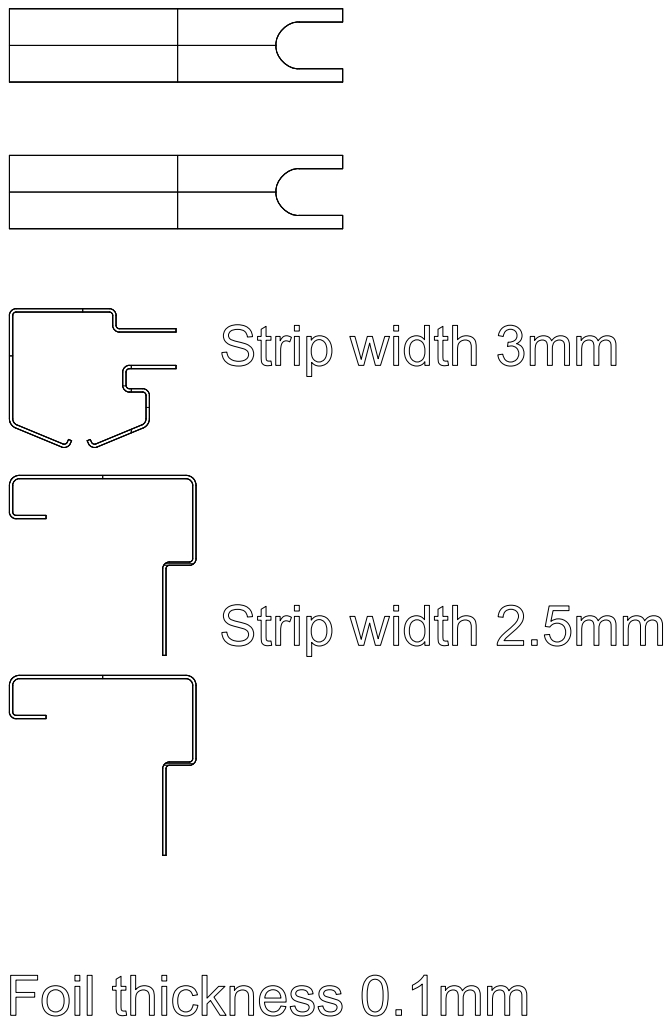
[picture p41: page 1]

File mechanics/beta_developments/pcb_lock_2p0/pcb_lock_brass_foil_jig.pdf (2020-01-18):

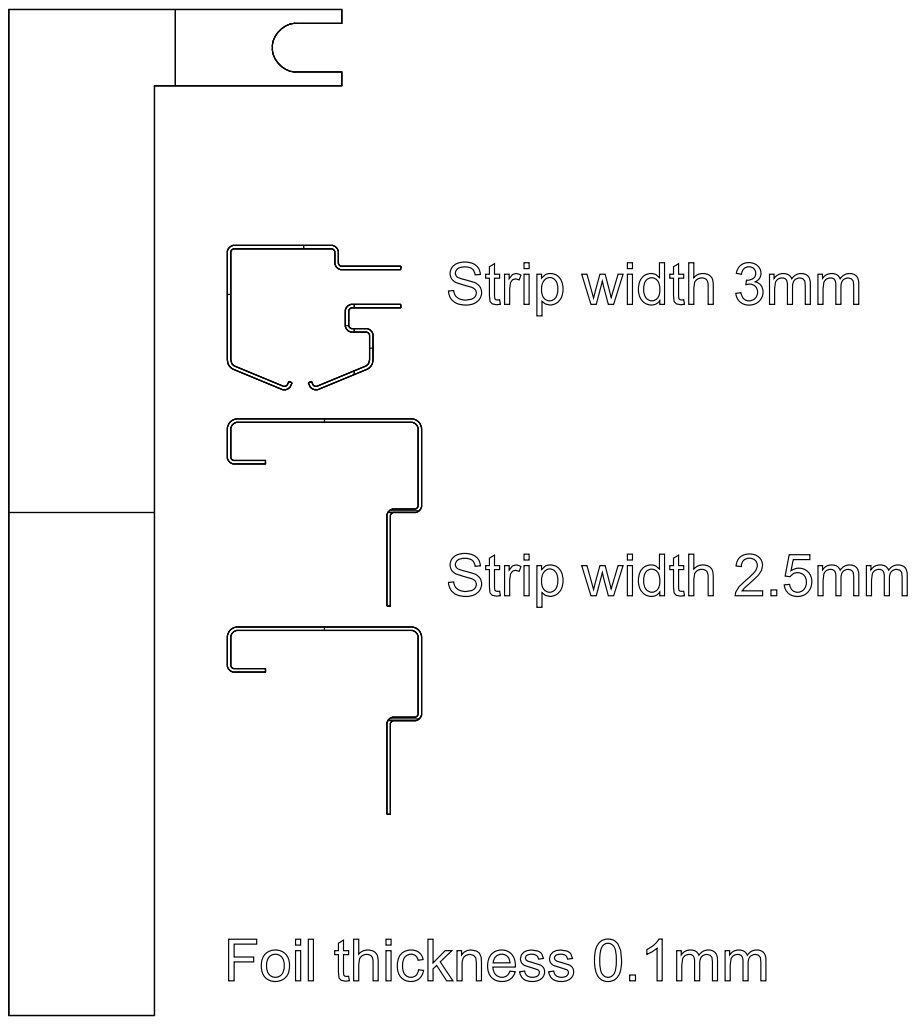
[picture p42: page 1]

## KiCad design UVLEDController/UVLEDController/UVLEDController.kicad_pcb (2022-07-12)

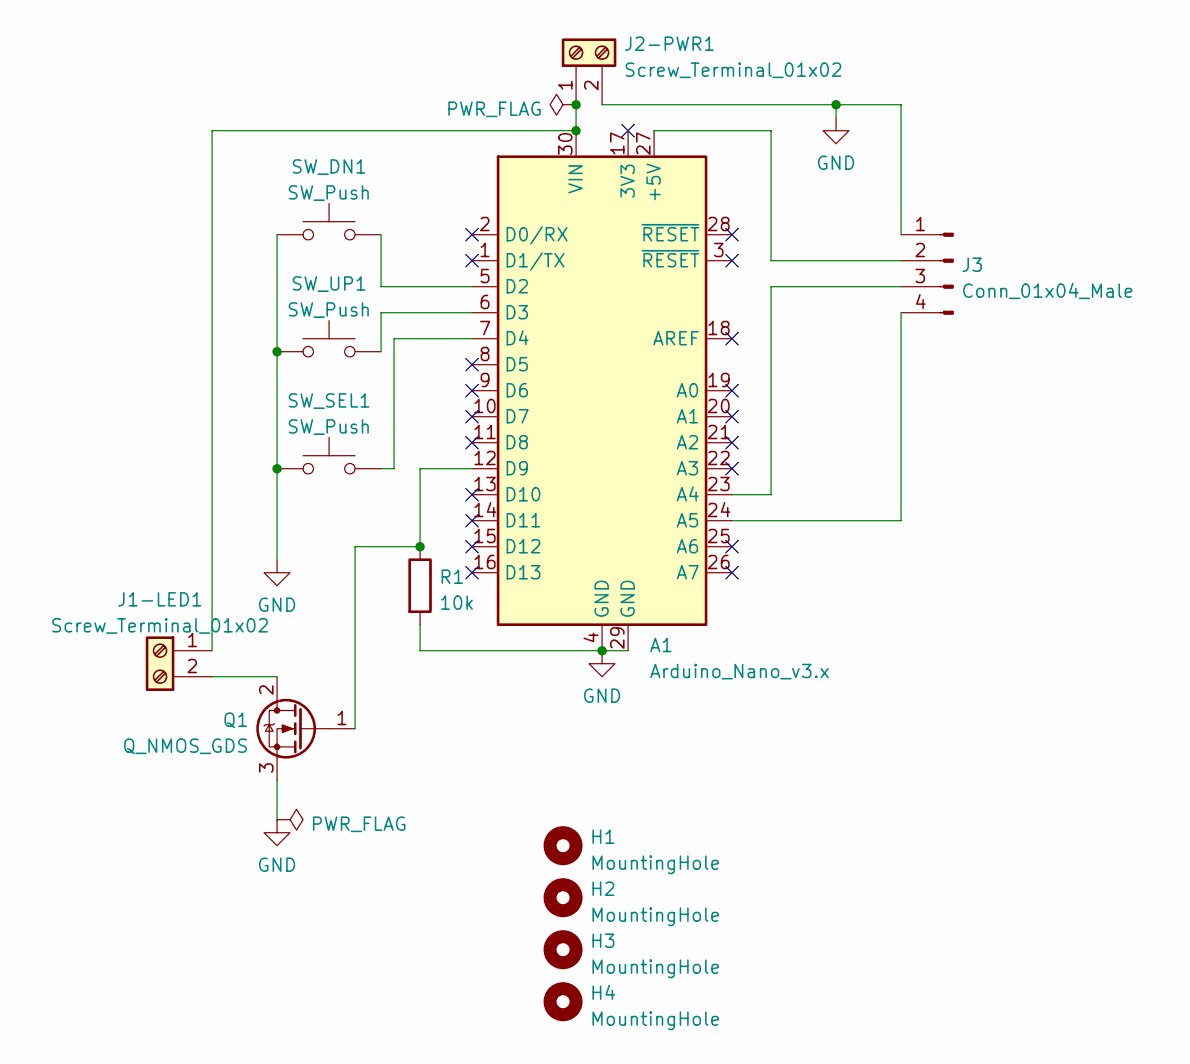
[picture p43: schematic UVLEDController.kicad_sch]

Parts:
A1: Arduino_Nano_v3.x; Arduino_Nano
H1, H2, H3, H4: MountingHole; MountingHole_3mm
J1-LED1, J2-PWR1: Screw_Terminal_01x02; TerminalBlock_Phoenix_PT-1,5-2-5.0-H_1x02_P5.00mm_Horizontal
J3: Conn_01x04_Male; PinHeader_1x04_P2.54mm_Horizontal
Q1: Q_NMOS_GDS; TO-220-3_Horizontal_TabUp
R1: 10k; R_0805_2012Metric_Pad1.20x1.40mm_HandSolder
SW_DN1: SW_Push; SW_PUSH_6mm
SW_SEL1: SW_Push; SW_PUSH_6mm
SW_UP1: SW_Push; SW_PUSH_6mm

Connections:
GND: A1.4 (GND), A1.29 (GND), J2-PWR1.2, J3.1, Q1.3 (S), R1.2, SW_DN1.1, SW_SEL1.1, SW_UP1.1
unnamed: A1.5 (D2), SW_DN1.2
unnamed: A1.6 (D3), SW_UP1.2
unnamed: A1.7 (D4), SW_SEL1.2
unnamed: A1.12 (D9), Q1.1 (G), R1.1
unnamed: A1.23 (A4), J3.3
unnamed: A1.24 (A5), J3.4
unnamed: A1.27 (+5V), J3.2
unnamed: A1.30 (VIN), J1-LED1.1, J2-PWR1.1
unnamed: J1-LED1.2, Q1.2 (D)

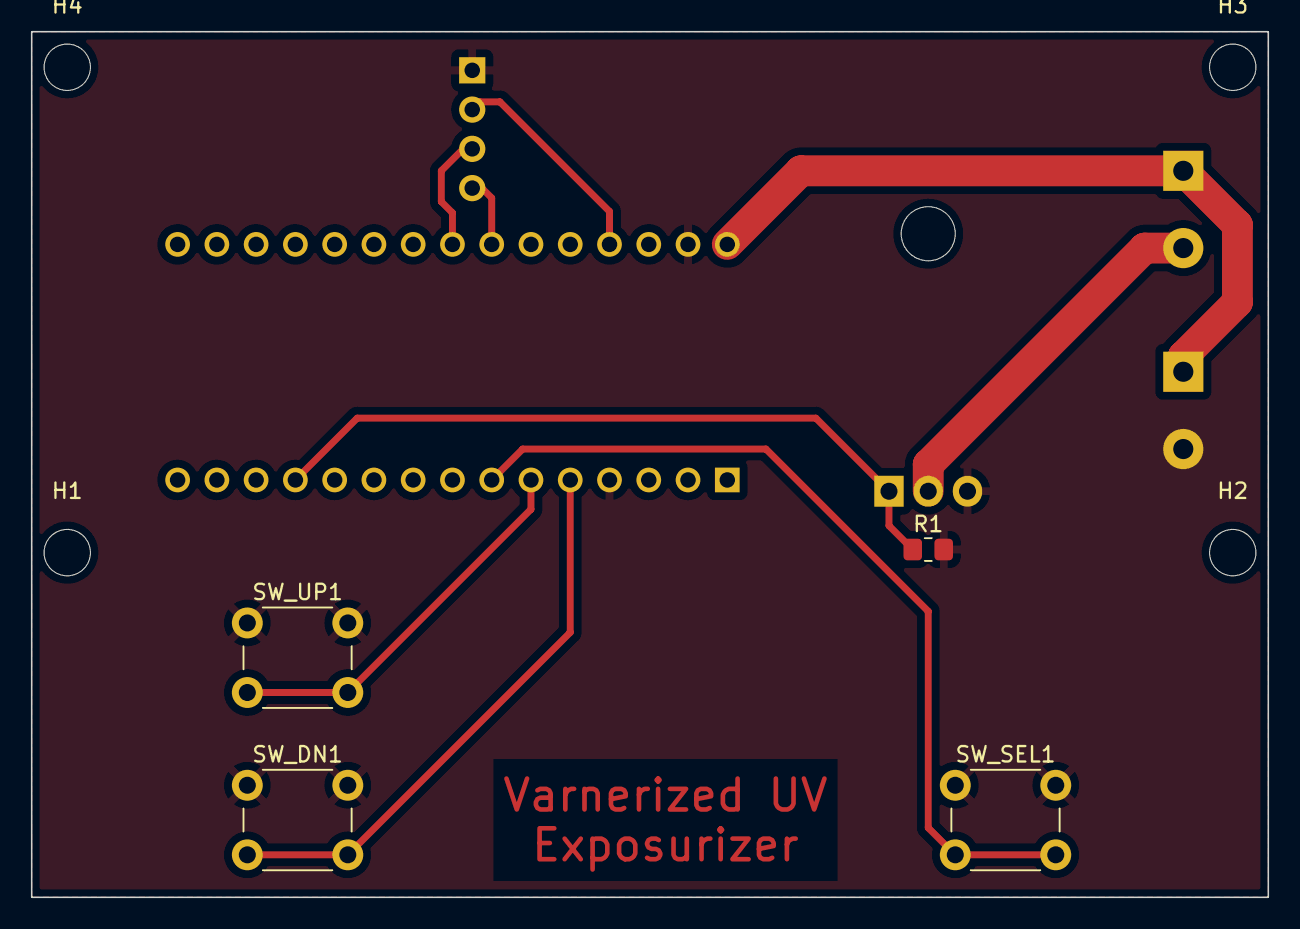
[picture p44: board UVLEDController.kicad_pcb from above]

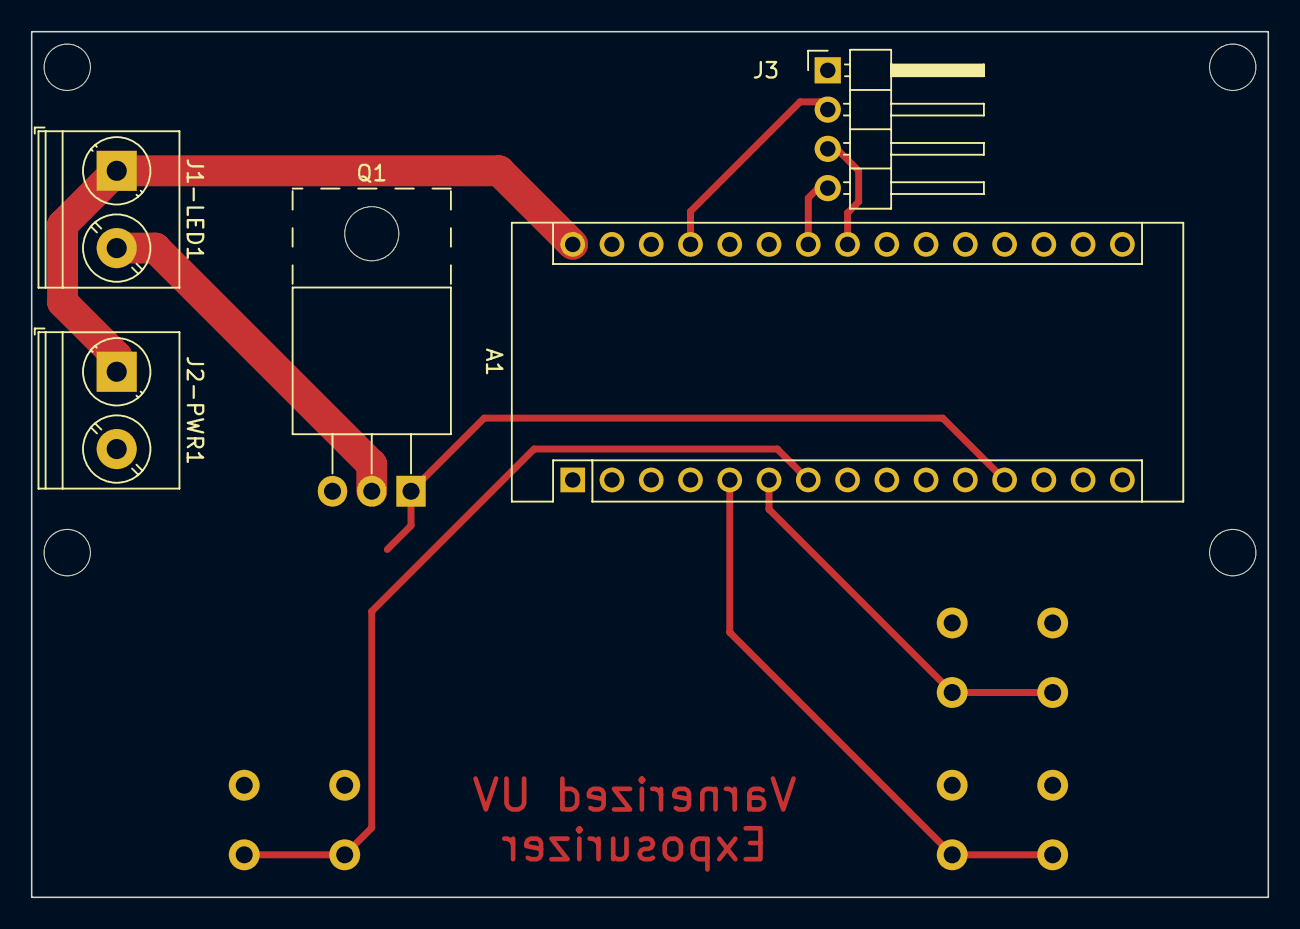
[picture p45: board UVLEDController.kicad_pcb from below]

Board: 2 copper layers, 80.0 x 56.0 mm, 13 parts (5 on the bottom side), 10 nets.

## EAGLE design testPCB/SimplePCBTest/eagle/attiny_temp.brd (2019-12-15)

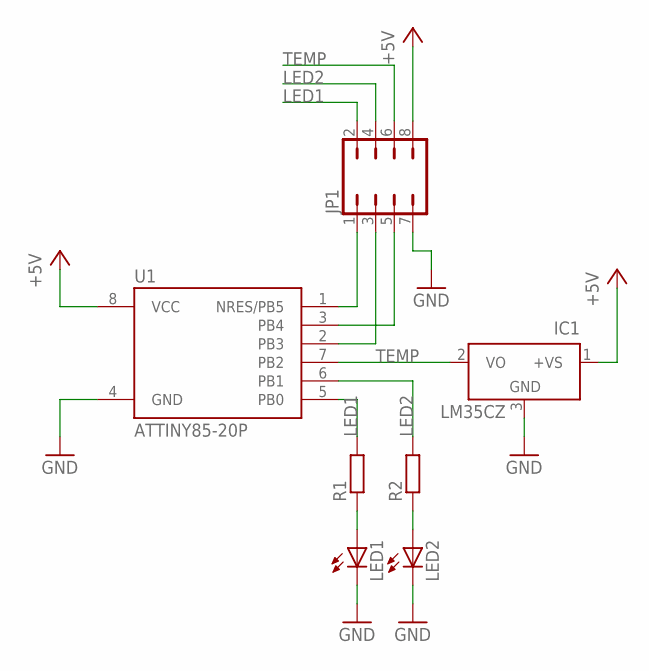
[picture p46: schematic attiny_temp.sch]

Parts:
IC1: LM35CZ; TO92
JP1: JP4Q
LED1, LED2: LEDCHIPLED_1206; CHIPLED_1206
R1, R2: R-EU_R1206; R1206
U1: ATTINY85-20P; PDIP08_300MIL

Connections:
+5V: IC1.1 (+VS), JP1.8, U1.8 (VCC)
GND: IC1.3 (GND), JP1.7, LED1.C, LED2.C, U1.4 (GND)
LED1: JP1.2, R1.2, U1.5 (PB0)
LED2: JP1.4, R2.2, U1.6 (PB1)
unnamed: LED1.A, R1.1
unnamed: LED2.A, R2.1
unnamed: JP1.1, U1.1 (NRES/PB5)
unnamed: JP1.3, U1.2 (PB3)
unnamed: JP1.5, U1.3 (PB4)
TEMP: IC1.2 (VO), JP1.6, U1.7 (PB2)

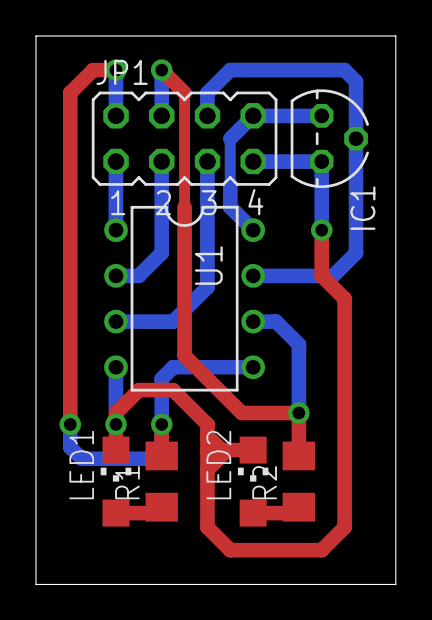
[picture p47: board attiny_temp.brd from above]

Board: 2 copper layers, 20.0 x 30.5 mm, 7 parts (0 on the bottom side), 10 nets.

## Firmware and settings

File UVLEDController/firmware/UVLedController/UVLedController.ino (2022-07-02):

#include <AceButton.h>
#include <LcdMenu.h>
#include <AsyncTimer.h>

#define LCD_ROWS 2
#define LCD_COLS 16

const int BTN_DN = 2; // D2
const int BTN_UP = 3; // D3
const int BTN_SEL = 4; // D4

const int LED_OUT = 9;

// Forward Declarations
void handleEvent(ace_button::AceButton*, uint8_t, uint8_t);
void enterExposure();
void enterIntensity();
void startExposure();
void stopExposure();



int exposure = 10; // TODO: Load from EEPROM.
int intensity = 255; // TODO: Load from EEPROM.

AsyncTimer timer;

extern MenuItem mainMenu[];

MenuItem mainMenu[] = {ItemHeader(),
                       ItemCommand("Exposure Time", enterExposure),
                       ItemCommand("Intensity", enterIntensity),
                       ItemCommand("Start", startExposure),
                       ItemFooter()};
LcdMenu menu(LCD_ROWS, LCD_COLS);

ace_button::AceButton btnDown(BTN_DN);
ace_button::AceButton btnUp(BTN_UP);
ace_button::AceButton btnSelect(BTN_SEL);


// valid modes 0 (menu), 1 (set exposure), 2 (set intensity), 3 (do exposing)
int mode = 0;

void setup() {
  pinMode(BTN_DN, INPUT_PULLUP);
  pinMode(BTN_UP, INPUT_PULLUP);
  pinMode(BTN_SEL, INPUT_PULLUP);
  pinMode(LED_OUT, OUTPUT);
  analogWrite(LED_OUT, 0);

  ace_button::ButtonConfig * config = btnUp.getButtonConfig();
  config->setEventHandler(handleEvent);
  config->setFeature(ace_button::ButtonConfig::kFeatureRepeatPress);

  config = btnDown.getButtonConfig();
  config->setEventHandler(handleEvent);
  config->setFeature(ace_button::ButtonConfig::kFeatureRepeatPress);

  config = btnSelect.getButtonConfig();
  config->setEventHandler(handleEvent);
  config->setFeature(ace_button::ButtonConfig::kFeatureClick);

  menu.setupLcdWithMenu(0x27, mainMenu);
}

void loop() {
  // Poll for input.
  btnDown.check();
  btnUp.check();
  btnSelect.check();
  timer.handle();
}

void enterExposure() {
  menu.hide();
  mode = 1;
  // Update the LCD:
  menu.lcd->clear();
  menu.lcd->setCursor(0, 0);
  menu.lcd->print("Exposure:");
  menu.lcd->setCursor(4, 1);
  menu.lcd->print(exposure);
}

void enterIntensity() {
  menu.hide();
  mode = 2;

  // Update the LCD:
  menu.lcd->clear();
  menu.lcd->setCursor(0, 0);
  menu.lcd->print("Intensity:");
  menu.lcd->setCursor(4, 1);
  menu.lcd->print(intensity);
}

void startExposure() {
  menu.hide();
  mode = 3;

  menu.lcd->setCursor(4, 0);
  menu.lcd->print("Exposing");

  analogWrite(LED_OUT, intensity);  
  timer.setTimeout(stopExposure, exposure * 1000);
}

void stopExposure() {
  analogWrite(LED_OUT, 0);
  mode = 0;
  menu.show();
}

void handleEvent(ace_button::AceButton* source, uint8_t eventType, uint8_t state) {
  if (eventType == ace_button::AceButton::kEventPressed && mode == 3) {
      stopExposure();
      timer.cancelAll();
      return;
  }

  
  if (source == &btnUp) {
    switch (eventType) {
      case ace_button::AceButton::kEventPressed:
      case ace_button::AceButton::kEventRepeatPressed:
        if (mode == 0) {
          menu.up();
        } else if (mode == 1) {
          exposure += 1;
          enterExposure();
        } else if (mode == 2 && intensity < 255) {
          intensity += 1;
          enterIntensity();
        }
        break;
    }
  } else if (source == &btnDown) {
    switch (eventType) {
      case ace_button::AceButton::kEventPressed:
      case ace_button::AceButton::kEventRepeatPressed:
        if (mode == 0) {
          menu.down();
        } else if (mode == 1 && exposure > 1) {
          exposure -= 1;
          enterExposure();
        } else if (mode == 2 && intensity > 1) {
          intensity -= 1;
          enterIntensity();
        }
        break;
    }
  } else if (source == &btnSelect) {
    switch (eventType) {
      case ace_button::AceButton::kEventClicked:
        if (mode == 0) {
          menu.enter();
        } else if (mode == 1 || mode == 2) {
          mode = 0;
          menu.show();
        }
        break;
    }
  }
}

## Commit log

2019-04-14 Small correction [skip ci]
    [Total_BOM_Ver_1_0_final.xlsx]
2019-04-14 Release v1.0. All step files released, added change tool, minor bug fixing [skip ci]
    [GT2_pulley_support_1p0.stl, GT2_pulley_support_1p0.stp, bed_holder_1p3.stp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]
2019-04-23 Added beta development folder and beta modified head 4p2 [skip ci].
    [head_4p2_beta.stl, head_4p2_beta.stp]
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2019-05-01 Correction of bug on limit switch debounce timer.
2019-05-13 Added Afro mini race spec as alternative ESC, other small BOM 1.0 corrections. [skip ci]
    [Total_BOM_Ver_1_0_final.xlsx]
2019-05-13 Correct wrong axis sign in system position after homing.
2019-05-15 ESC bullet connectors note[skip ci]
    [Total_BOM_Ver_1_0_final.xlsx]
2019-07-21 Improved versions of Head and Bridge added in mechanics release folders. [skip ci]
    [Total_BOM_Ver_1_0_1.xlsx, bridge_2p2.stl, bridge_2p3_a.stl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]
2019-08-24 Specified use of 16 and 26 AWG cables. [skip ci]
    [Total_BOM_Ver_1_0_1.xlsx, Total_BOM_Ver_1_0_final.xlsx]
2019-09-29 Added Cutterpillar design files and related info.
    [bridge_and_head_assembly_print_1p0.step, bridge_and_head_assembly_print_1p0.stl]
2019-09-30 Files moved to cutterpilla folder.[skip ci]
    [bridge_and_head_assembly_print_1p0.step, bridge_and_head_assembly_print_1p0.stl]
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2019-12-15 Added simple PCB Test [skip ci].
    [attiny_temp.brd, attiny_temp.sch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]
2019-12-24 Adding Solder Mask Add-On part. [skip ci]
    [laser_soldermask_beta_1p0.step, laser_soldermask_beta_1p0.stl]
2020-01-12 Correction on spindle stop function, the pwm output is frozen to zero, instead of disabling it (high impedance state)
2020-01-12 New PCB Holder design files in beta [skip ci]
    [pcb_lock_2p2.step, pcb_lock_2p2.stl, pcb_lock_frame_to_bed_connection_1p0.step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]
2020-01-18 Correction of pdf files for pcb lock 2.0[skip ci]
2020-01-22 BOM for the new PCB holder [skip ci].
    [BOM_pcb_lock_2p0.xlsx]
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2020-02-09 Specified JST PH 2.0 in the BOMs files. [skip ci]
    [Total_BOM_Ver_1_0_1.xlsx, Total_BOM_Ver_1_0_final.xlsx]
2020-02-09 Added important note on tags and release notes in the BOMs files. [skip ci]
    [Total_BOM_Ver_1_0_1.xlsx, Total_BOM_Ver_1_0_final.xlsx]
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2020-12-27 Modified heartbeat led initialization. [skip ci]
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2021-02-06 Moved betas accepted or substituted to old_beta_developments folder. [skip ci]
    [BOM_pcb_lock_2p0.xlsx, head_4p2_beta.stl, head_4p2_beta.stp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]
2021-02-06 New HEAD with NEMA8 motor, pcb lock, bridge_b and cable chain. [skip ci]
    [BOM_bridge_2p4_b.xlsx, BOM_chain_1p0.xlsx, BOM_head_4p3.xlsx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]
2021-05-22 Fixed STL.
    [bridge_2p4_b.stl]
2021-06-02 Ramping avoided if the new pwm is equal to current pwm.
2021-10-18 Modified the right and left bridge to use an 8mm rod.
    [Bridge Left.step, Bridge Left.stl, Bridge Right.step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]
2021-10-18 Upper bridge 8mm beam repositioned 1mm up, to make room for the belt on the right side.
    [Bridge Left.step, Bridge Left.stl, Bridge Right.step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]
2021-10-18 Updated some docs. NEMA 17 Motor mount. Mirror for other side.
    [motor_holder_1p0.stl, motor_holder_1p0.stp, nema17_motor_mount.stl]
2021-10-19 Pushing updates to start print analysis.
    [Belt Clamp.stl, Bridge Bottom Cap.stl, Bridge Core.stl]
2021-10-19 First attempt at GT2 Pulleys using 683ZZ bearings. Checking in a few 3mf projects that I'll be testing as well.
    [Bridge Core.3mf, Bridge Core_Test.3mf, GT2-16-Pully_Idler.stl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]
2021-10-20 After a few tweaks, the GT2 pulleys seem to work. Need to rename the files.
    [GT2-16-Pully_Idler.stl, GT2-16-Smooth-Pully_Idler.stl, Pulley_T-MXL-XL-HTD-GT2_N-tooth.scad]
2021-10-20 Renamed the files since I have a mental block on how pulley is spelled.
    [GT2-16-Pulley_Idler.stl, GT2-16-Smooth-Pulley_Idler.stl]
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2021-10-20 Bridge Core Test Update.
    [Bridge Core_Test.3mf]
2021-10-20 Added the 3mf from tuning my PETG for pulley production.
    [GT2-16-Pulley.3mf]
2021-10-20 * Converted all Bridge fasteners to pocketed M3 hex nuts, rather than square nuts on the back. * LM8UU * Slightly larger hole size. * Cutout for flex expansion / compression around bearings. The M3x3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
    [Belt Clamp.stl, Bridge Bottom Cap.stl, Bridge Core.stl]
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2021-10-21 Update to the shim washer for the pulleys.
    [Pulley_washer.scad, Pulley_washer.stl]
2021-10-22 Update to the pulley washer to use the outer diameter specificed by the ANT project.
    [Belt Holder.3mf, Pulley_washer.scad, Pulley_washer.stl]
2021-10-22 * Parametric bridge bottom cap modifications. :-)
    [Bridge Bottom Cap.stl, Parametric Bridge Bottom v0.f3d]
2021-10-23 * Updated the bridget bottom cap to use better constraints now that I understand sketches better. :-) * Designed a new head for use with a D-Power Series D2826 1000KV motor, and TR8 leadscrew with to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
    [Bridge Bottom Cap.stl, D2826 TR8 LM8UU Head.stl]
2021-10-23 3mf for the bridge bottom
    [Bridge Bottom.3mf]
2021-10-23 * Core bottom: added a few fillets to match the core. * Core: Added fillets to improve printability when rotated to maintain proper diameter for the LM8UU bearings. * Head: Fitment fixes * Adjusted p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
    [Bridge Bottom Cap.stl, Bridge Core.stl, D2826 TR8 LM8UU Head.stl]
2021-10-23 Mirrored the NEMA mounts.
    [NEMA17_Mount_Left.stl, NEMA17_Mount_Right.stl, nema17_motor_mount.3mf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]
2021-10-26 PARAMETRIC, CONSTRAINED CAD MODELS FOR THE WIN!
    No really, re-implemented the bridge and head assembly in Fusion360 as parametric models. So awesome. Much Wow.
    So this is the first STL dump of that work, which sets up the head to use an inexpensive D2826 BLDC and TR8x8 leadscrew on a 1:3.5 reduction driven from a NEMA17 mounted up top.
    [Belt Clamp.stl, Belt Holder.3mf, Bridge Bottom Cap.stl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]
2021-10-26 * Y-axis bridge parts * Fixed spacing issue for mount hole locations. * Corrected the lack of counterboring. * Adjusted orientation of the M3 nut cutout for the idler bearings. * Fixed small issue on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
    [bridge_upper_8mm.stl, bridge_y_axis_left_8mm.stl, bridge_y_axis_right_8mm.stl]
2021-10-26 * Fitment adjustments of M3 nut pockets.
    [belt_holder.stl, bridge_upper_8mm.stl, bridge_y_axis_left_8mm.stl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]
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2021-10-28 Improved the room for the NEMA head mount hex nuts. I was able to use the first printed head by heating up square nuts and melting them into position.
    [bridge_upper_8mm.stl]
2021-10-28 Refinements for Fit.
    * Bridge core modifications based on print output.
    * bridge nema_17 rotation angle for tension adjusted (added 5 more degrees) of rotation.
    * Bridge upper embedded nuts modified to proper thickness for M3 hex nuts.
    [bridge_core_8mm.stl, bridge_lower_8mm.stl, bridge_nema17_mount_tr8.stl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]
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2021-10-28 Fixed a missing face for an extrude.
    [bridge_nema17_mount_tr8.stl]
2021-10-28 * Adjusted the wire escapement for the z-limit switch.
    [bridge_upper_8mm.stl]
2021-10-29 Added a 48 tooth pulley, since the 56 is a bit... too big.
    [gt2_48tooth_drive_pulley.stl]
2021-10-29 Adding a 50-tooth pulley, which should fit better for the 140 tooth belt lenght, and 1:3.125 gives an even number of steps/mm that doesn't end with a non-repeating decimal for fractional depths. :-)
    [gt2_50tooth_drive_pulley.stl]
2021-10-29 Updated the README with the calculations for the Z-axis design.
    [bridge_core_8mm.3mf, bridge_lower_8mm.3mf, bridge_nema17_mount_tr8.3mf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]
2021-10-29 * Added a spacer for the GT2 drive pulley on the z-axis, so that it can bear against the upper and lower bearings. * Added 6mm height to the upper bridge to compensate for the necessary 6mm added to 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
    [bridge_upper_8mm.stl, gt2_50tooth_drive_pulley.stl, gt2_pulley_spacer.stl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]
2021-10-30 * Updates to the head to completely encase the LM8UU bearings. * Auto increase the upper bridge height to compensate for different linear bearing lengths. * Adjust position of the outrunner motor bas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
    [bridge_nema17_mount_tr8.stl, bridge_upper_8mm.stl, head_8mm_D2826_TR8.stl]
2021-10-30 Fixed the missing bearing / shaft bore in the head, and moved the Z-nut back down to 4mm.
    [head_8mm_D2826_TR8.stl]
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2021-11-05 Adjust the back electronics housing for an UNO R3, and make it M3x40 friendly. Remove the firmware. I'm storing that in a separate repo.
    [Support1.stl, Support2.stl, uno_back.stl]
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2021-11-05 Fixes for the bridge anchor.
    [Bridge Anchor.stl, Bridge Anchor65.stl]
2021-11-06 Intermediate re-organization of mechanical folder: copied parts file from beta development, removed old versions. Missing BOM updates and other modifications. [skip ci]
    [bridge_2p3_b.stl, bridge_2p3_b.stp, bridge_2p4_b.stl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]
2021-11-06 Intermediate re-organization of mechanical folder: changed pcb_lock_brass_foil_jig and updated version of bed holder with one part that is now in pcb_lock_frame_to_bed_connection_1p0. Missing BOM upd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
    [bed_holder_1p3.stp, bed_holder_1p4.stl, bed_holder_1p4.stp]
2021-11-06 The_Ant_version_1_1_0 release [skip ci]
    [BOM_bridge_2p4_b.xlsx, BOM_chain_1p0.xlsx, BOM_head_4p3.xlsx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]
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2021-11-09 Drive belt redesign and upper bridge tweak.
    [18ID_Drive_Belt.stl, 20ID_Drive_Belt.stl, bridge_upper_8mm.stl]
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2021-11-10 Added zip tie points to the cable chain mount.
    [CableChain_FrameMount.stl]
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2021-11-14 Updated to give a bit more space for the nuts to enable sliding, and to move the conductor holes in the hold-down.
    [Front Bracket.stl, HoldDown.stl, Right Bracket.stl]
2021-11-15 Fixed the right bracket lack of counterbore
    [Right Bracket.stl]
2021-11-19 Rather Major update to address some fitment issues.
    * 5.5mm camera clamp. Parameter added.
    * Moved the z-axis nut and screw position to no longer interferre with the camera.
    * Added a 30mm screw to help clamp the z-axis motor mount and bridge together, resisting upward motion of the z-axis.
    * Made the bridge and motor mount a bit more stiff around the 22mm bearings to help resist vertical motion.
    * Revised the sketches for a few components to better constrain them.
    * The head's limit-switch screw hole should be able to recess now.
    [Bridge Anchor.stl, bridge_nema17_mount_tr8.stl, bridge_upper_8mm.stl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]
2021-11-19 Found some missing geometry on the head.
    [head_8mm_D2826_TR8.3mf]
2021-11-19 Forgot it exports in 3mf by default. Yick.
    [head_8mm_D2826_TR8.3mf, head_8mm_D2826_TR8.stl]
2021-11-21 * Camera offset now 15x5, to avoid interference between the clamp and the spindle belt. * Fixed a missing volume in the upper bridge.
    [bridge_upper_8mm.stl, head_8mm_D2826_TR8.stl]
2021-12-13 The_Ant_version_1_1_0 release fixed. [skip ci]
    [bridge_2p4_b.stl, bridge_2p4_b.stp]
2022-02-15 Adding a re-do of the frame to pcb lock connections. Vertical orientation, wider stuff, integrated LED & resistor mounts.
    [pcb_lock_frame_to_bed_connection_2p0.stl]
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2022-07-02 Updates for physical dimensions based on Fuseion360 test fits.
    [UVLEDController.kicad_pcb, UVLEDController.kicad_sch, UVLEDController.step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]
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2022-07-02 Moved the screw terminals to a better location. Tweaked position of i2c header.
    [UVLEDController.kicad_pcb, UVLEDController.kicad_sch, UVLEDController.step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]
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2022-07-15 Modifications for mounting / creating a cabinet to sit beneath the Varnerized ANT. * UV Curing bay. * Intensity (PWM) & Timer controlled by Arduino. * PSU Shroud Holds all circuitry. * KiCad project 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
    [BedContactor.3mf, BedContactor.stl, BedContactorFoilRetainer.stl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]
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
